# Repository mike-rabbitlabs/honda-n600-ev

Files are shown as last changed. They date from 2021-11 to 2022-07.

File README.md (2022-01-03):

# Honda N600 EV Conversion

All control systems and dash UI code.

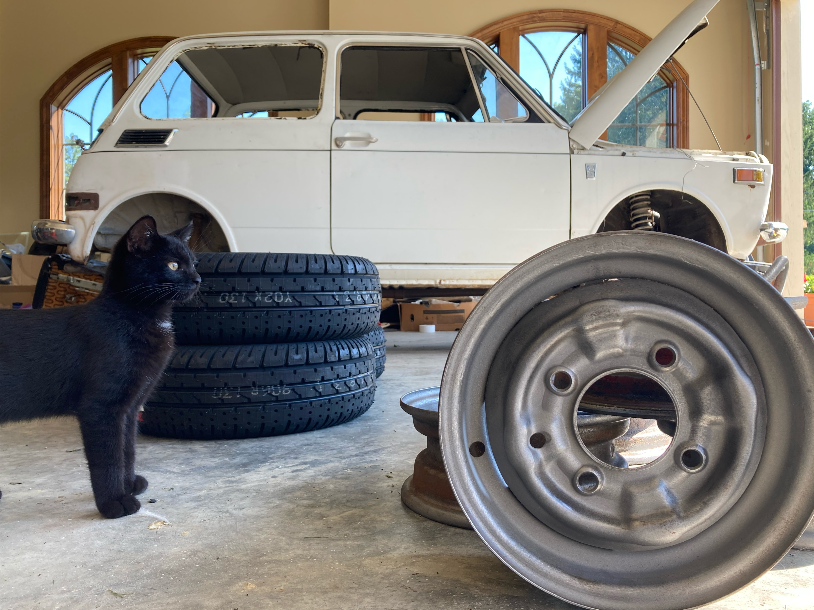
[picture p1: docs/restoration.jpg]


## Master Control Unit
Communicates (via CAN) to the BMS, controls fan, and coolant pumps, monitors temperature.

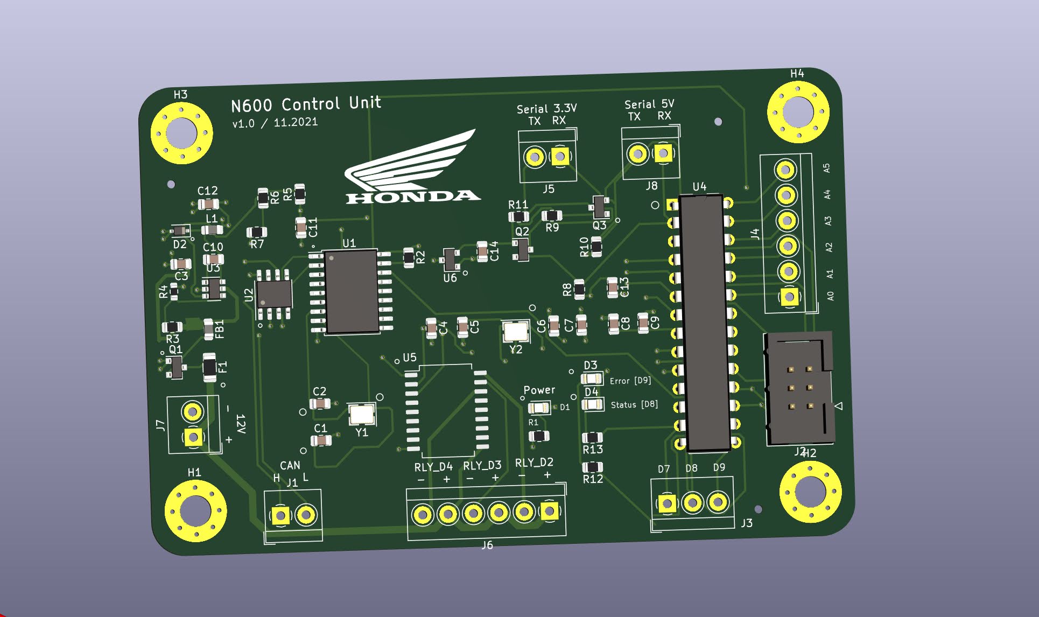
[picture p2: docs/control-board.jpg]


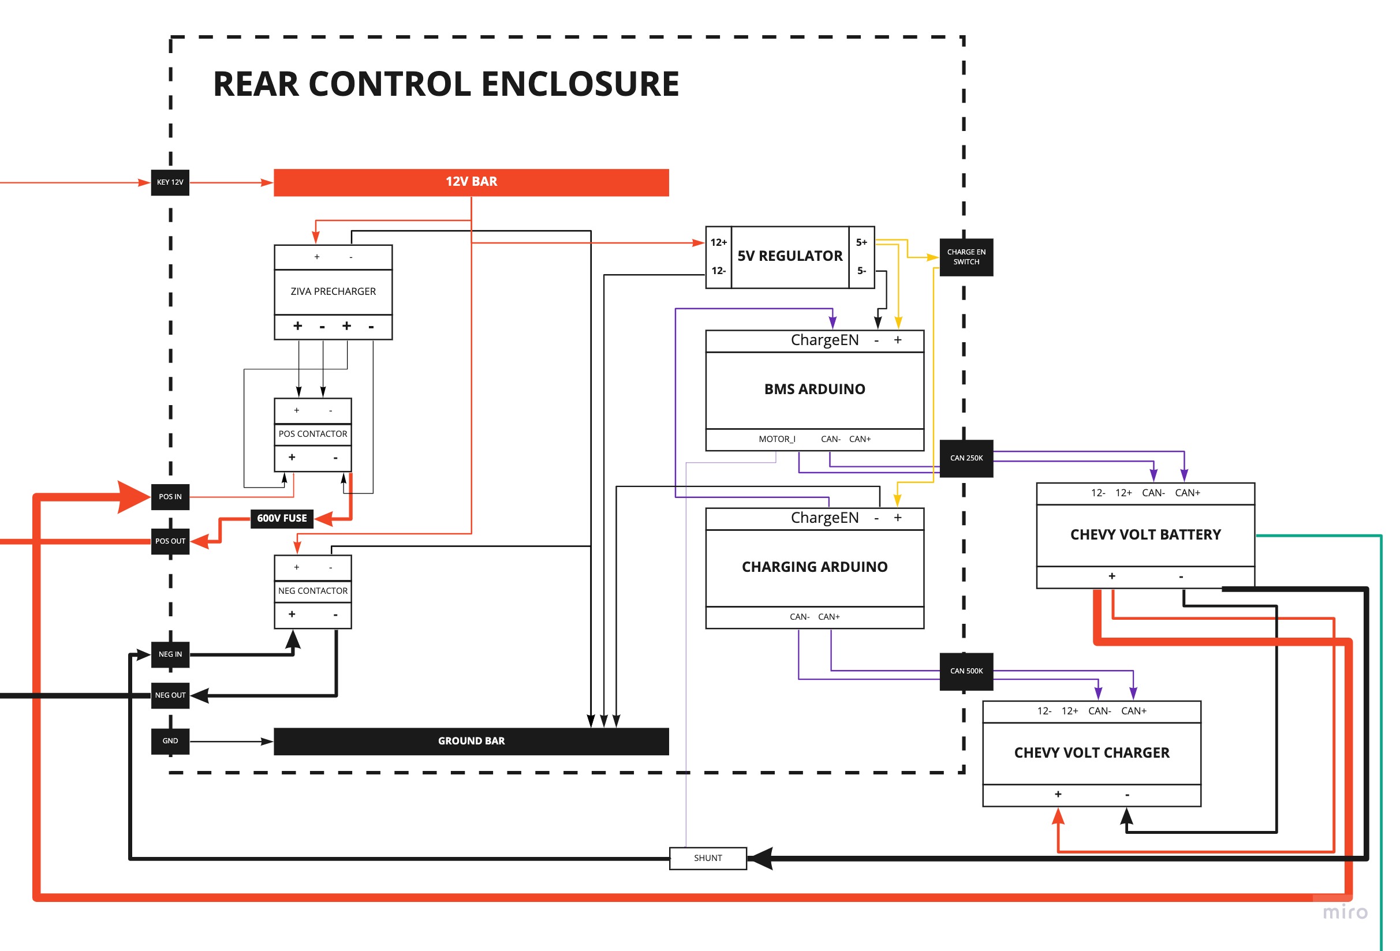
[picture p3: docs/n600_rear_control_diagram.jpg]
System Diagram


## Dash Screen UI

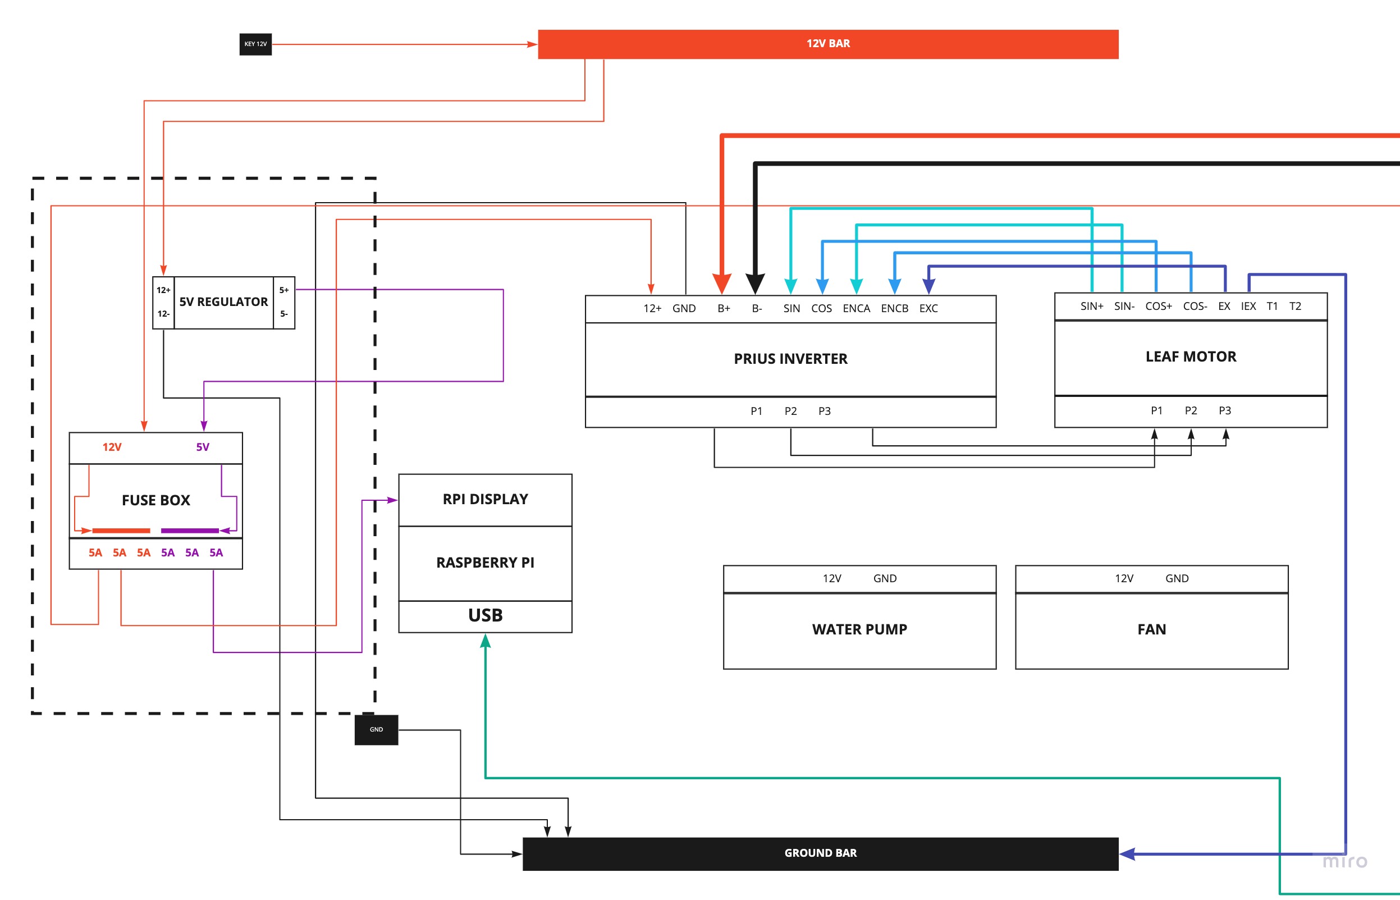
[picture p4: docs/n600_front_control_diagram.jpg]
System Diagram


### Requirements

* [Kikad](https://www.kicad.org/)
* [Node.js/NPM](https://nodejs.org/en/download/)

### Progress
* [Leaf EM61 Motor running with Prius Gen3 inverter](https://youtu.be/WkFnErgvj8M)
* [Raspberry Pi dash screen](https://youtu.be/67Cg47E4874)
* CAN communication with chevy volt bms
* CAN communication with chevy volt charger

### Dev Setup

* Within the dash-screen/server directory, Run: _npm install_ to download dependencies
* Within the dash-screen/ui directory, Run: _npm install_ to download dependencies
* Run: _npm start_ within the dash-screen/ui directory
* Run: _npm start_ within the dash-screen/server directory
* After the build process finishes, you should see a chrome popup to http://localhost:3001
* Frontend will auto reload on ui code changes

### Production Setup
* Build the app from within the dash-screen/server directory with: _npm run build_ (builds both the frontend and hosts from the compiled react app from the app server)
* The server should now host the react app at localhost:5000 (when running the server with _npm start_)
* Configure the docker-compose.yml file with your chose parameters, and run _docker-compose up_ to start the production server

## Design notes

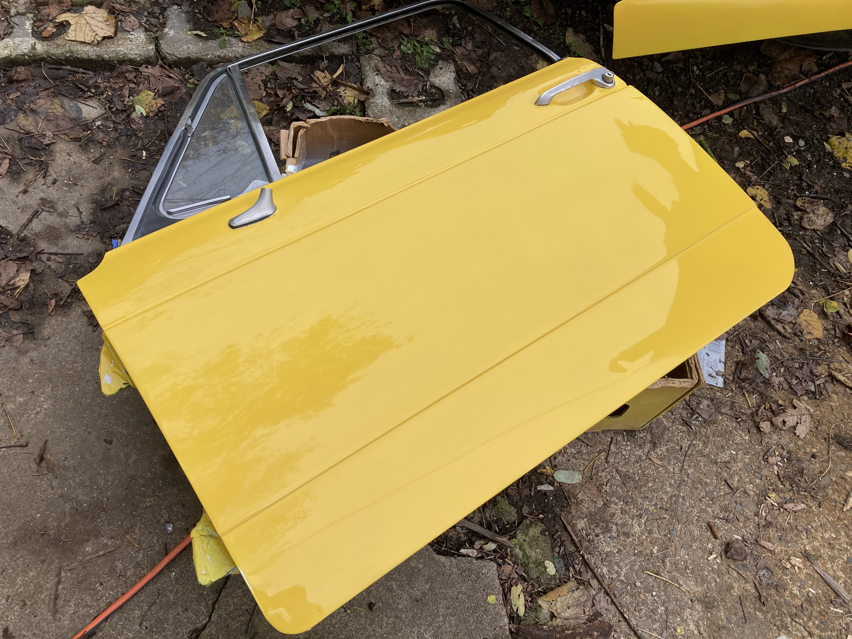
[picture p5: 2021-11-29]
docs/paint2.JPG

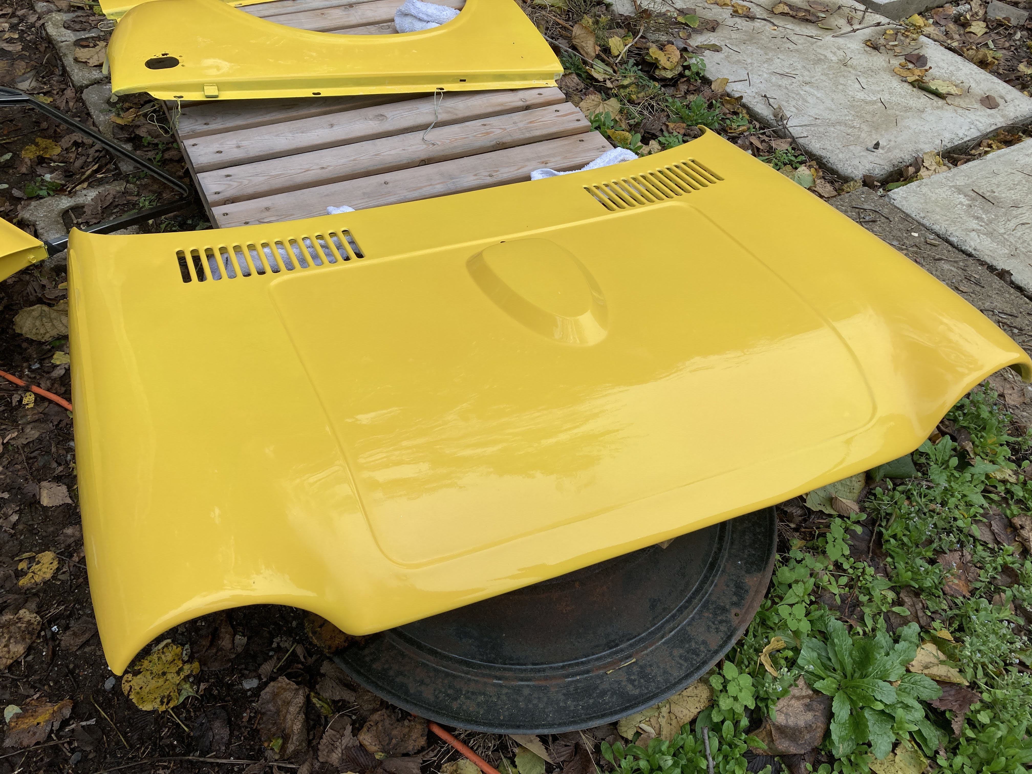
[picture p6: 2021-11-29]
docs/paint1.jpg

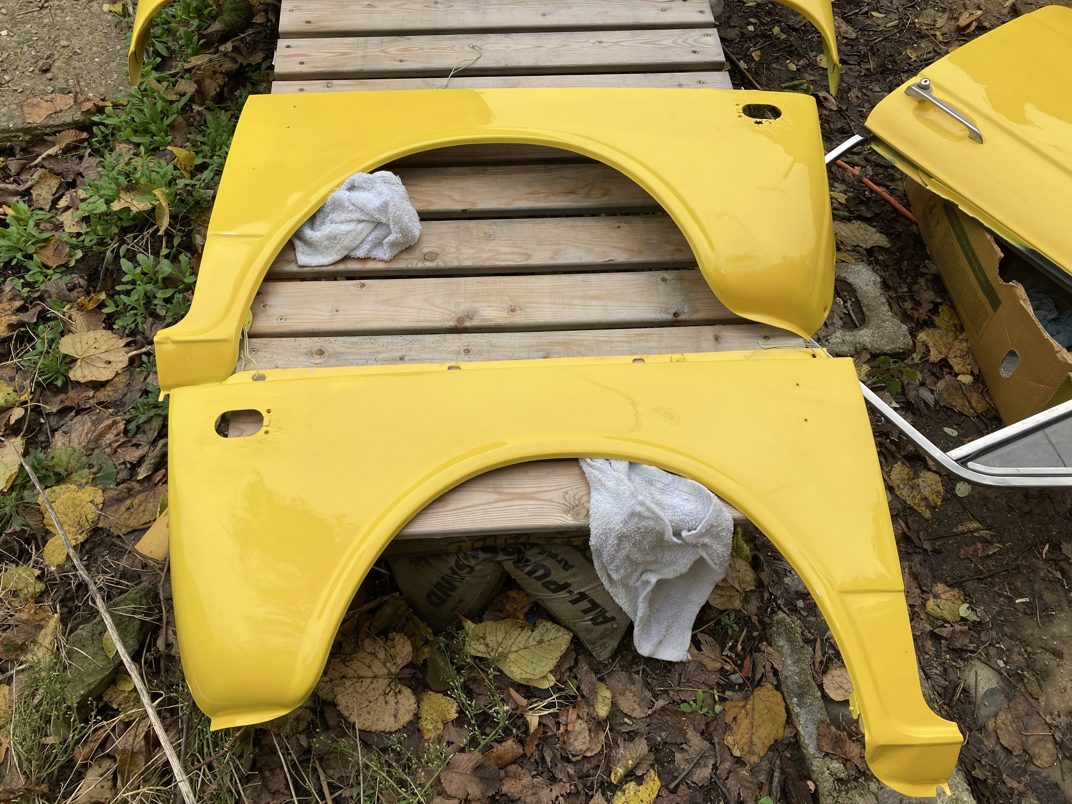
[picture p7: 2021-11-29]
docs/paint3.JPG

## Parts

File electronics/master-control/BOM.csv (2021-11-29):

Designator | Quantity | Comment | Footprint | Datasheet | JLCPCB Part #
C10 | 1 | 10nF | Capacitor_SMD:C_0805_2012Metric | ~ | C1710
C13 C14 | 2 | 1uF | Capacitor_SMD:C_0805_2012Metric | ~ | C28323
C3 C11 C12 | 3 | 10uF | Capacitor_SMD:C_0805_2012Metric | ~ | C15850
C1 C2 C4 C5 | 4 | 22pF | Capacitor_SMD:C_0805_2012Metric | ~ | C1804
C6 C7 C8 C9 | 4 | 100nF | Capacitor_SMD:C_0805_2012Metric | ~ | C49678
D1 D3 D4 | 3 | LED | LED_SMD:LED_0805_2012Metric | ~ | C84256
D2 | 1 | 1N5819 | Diode_SMD:D_SOD-323 | http://www.vishay.com/docs/88525/1n5817.pdf | C191023
F1 | 1 | 250mA | Fuse:Fuse_1206_3216Metric | ~ | C135334
FB1 | 1 | 600 @ 600Mhz | Inductor_SMD:L_0805_2012Metric | ~ | C1017
H1 H2 H3 H4 | 4 | MountingHole | MountingHole:MountingHole_4.3mm_M4_Pad_Via | ~
J1 J5 J7 J8 | 4 | Screw_Terminal_01x02 | TerminalBlock_4Ucon:TerminalBlock_4Ucon_1x02_P3.50mm_Horizontal | ~
J2 | 1 | AVR-ISP-6 | Connector_IDC:IDC-Header_2x03_P2.54mm_Vertical | ~
J3 | 1 | Screw_Terminal_01x03 | TerminalBlock_4Ucon:TerminalBlock_4Ucon_1x03_P3.50mm_Horizontal | ~
J4 J6 | 2 | Screw_Terminal_01x06 | TerminalBlock_4Ucon:TerminalBlock_4Ucon_1x06_P3.50mm_Horizontal | ~
L1 | 1 | 10u | Inductor_SMD:L_0805_2012Metric | ~ | C1046
Q1 | 1 | AO3401A | Package_TO_SOT_SMD:SOT-23 | http://www.aosmd.com/pdfs/datasheet/AO3401A.pdf | C15127
Q2 Q3 | 2 | 2N7002 | Package_TO_SOT_SMD:SOT-23 | https://www.onsemi.com/pub/Collateral/NDS7002A-D.PDF | C8545
R1 R12 R13 | 3 | 1.2K | Resistor_SMD:R_0805_2012Metric | ~ | C17379
R2 R8 R9 R10 R11 | 5 | 10K | Resistor_SMD:R_0805_2012Metric | ~ | C17414
R3 | 1 | 100K | Resistor_SMD:R_0603_1608Metric | ~ | C25803
R4 | 1 | 40K | Resistor_SMD:R_0603_1608Metric | ~ | C4197
R5 | 1 | 75K | Resistor_SMD:R_0805_2012Metric | ~ | C17819
R6 | 1 | 13K | Resistor_SMD:R_0805_2012Metric | ~ | C17455
R7 | 1 | 2.4K | Resistor_SMD:R_0805_2012Metric | ~ | C17526
U1 | 1 | MCP2515-xSO | Package_SO:SOIC-18W_7.5x11.6mm_P1.27mm | http://ww1.microchip.com/downloads/en/DeviceDoc/21801e.pdf
U2 | 1 | TJA1051T | Package_SO:SOIC-8_3.9x4.9mm_P1.27mm | http://www.nxp.com/documents/data_sheet/TJA1051.pdf | C6952
U3 | 1 | MP2359-DJ | Package_TO_SOT_SMD:SOT-23-6
U4 | 1 | ATmega328P-PU | Package_DIP:DIP-28_W7.62mm | http://ww1.microchip.com/downloads/en/DeviceDoc/ATmega328_P%20AVR%20MCU%20with%20picoPower%20Technology%20Data%20Sheet%2040001984A.pdf
U5 | 1 | ULN2803A | Package_SO:SOP-18_7x12.5mm_P1.27mm | http://www.ti.com/lit/ds/symlink/uln2803a.pdf | C845537
U6 | 1 | XC6206PxxxMR | Package_TO_SOT_SMD:SOT-23 | https://www.torexsemi.com/file/xc6206/XC6206.pdf | C5446
Y1 Y2 | 2 | 16Mhz | Crystal:Crystal_SMD_3225-4Pin_3.2x2.5mm | ~ | C13738

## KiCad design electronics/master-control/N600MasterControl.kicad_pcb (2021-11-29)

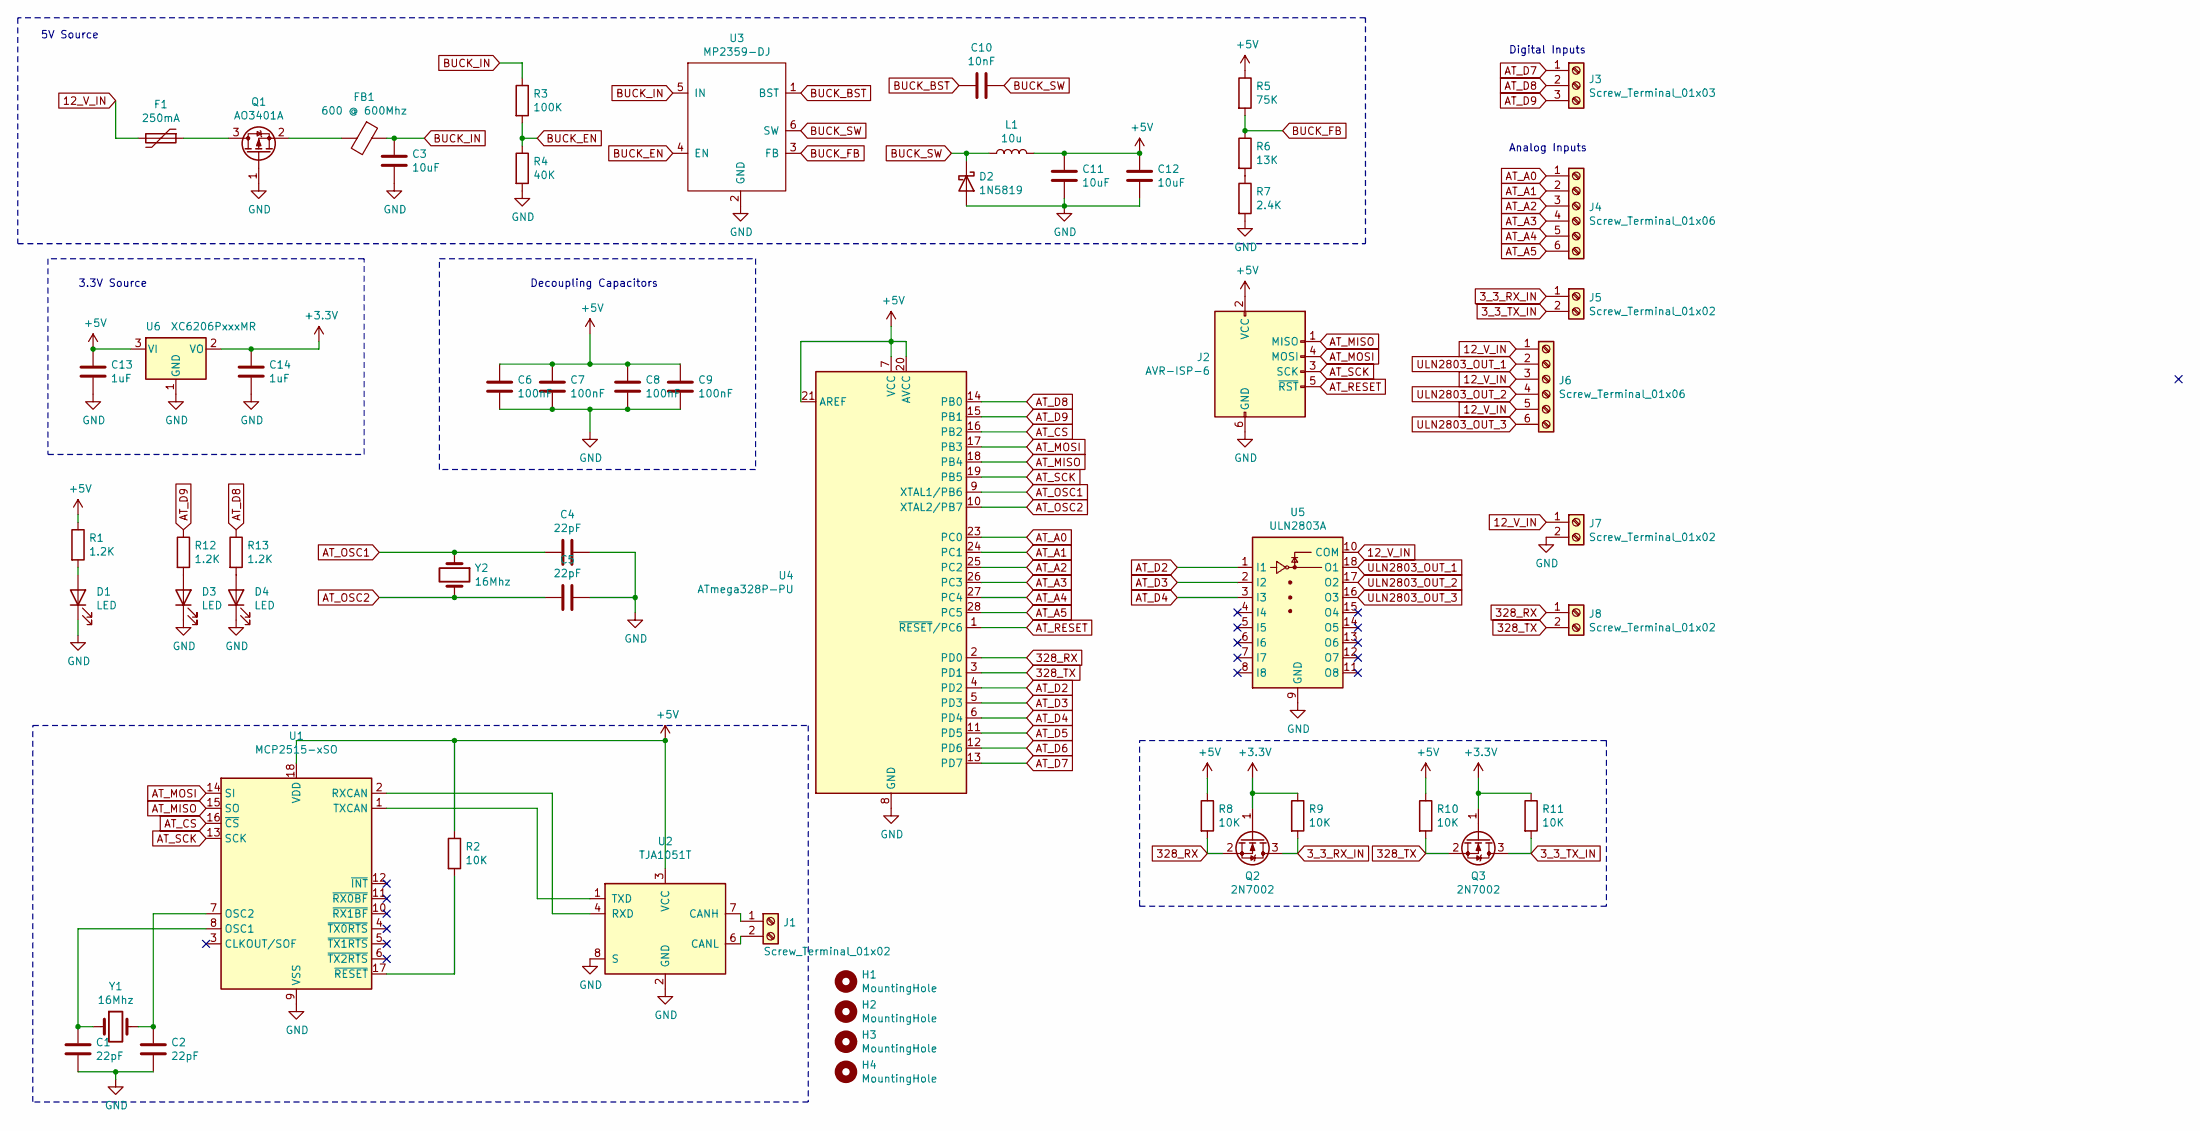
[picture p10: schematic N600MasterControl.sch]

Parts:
C1, C2, C4, C5: 22pF; C_0805_2012Metric; JLCPCB Part # C1804
C3, C11, C12: 10uF; C_0805_2012Metric; JLCPCB Part # C15850
C6, C7, C8, C9: 100nF; C_0805_2012Metric; JLCPCB Part # C49678
C10: 10nF; C_0805_2012Metric; JLCPCB Part # C1710
C13, C14: 1uF; C_0805_2012Metric; JLCPCB Part # C28323
D1: LED; LED_0805_2012Metric; JLCPCB Part # C84256
D2: 1N5819; D_SOD-323; JLCPCB Part # C191023
D3: LED; LED_0805_2012Metric; JLCPCB Part # C2297
D4: LED; LED_0805_2012Metric; JLCPCB Part # C2293
F1: 250mA; Fuse_1206_3216Metric; JLCPCB Part # C135334
FB1: 600 @ 600Mhz; L_0805_2012Metric; JLCPCB Part # C1017
H1, H2, H3, H4: MountingHole; MountingHole_4.3mm_M4_Pad_Via
J1, J5, J7, J8: Screw_Terminal_01x02; TerminalBlock_4Ucon_1x02_P3.50mm_Horizontal
J2: AVR-ISP-6; IDC-Header_2x03_P2.54mm_Vertical
J3: Screw_Terminal_01x03; TerminalBlock_4Ucon_1x03_P3.50mm_Horizontal
J4, J6: Screw_Terminal_01x06; TerminalBlock_4Ucon_1x06_P3.50mm_Horizontal
L1: 10u; L_0805_2012Metric; JLCPCB Part # C1046
Q1: AO3401A; SOT-23; JLCPCB Part # C15127
Q2, Q3: 2N7002; SOT-23; JLCPCB Part # C8545
R1, R12, R13: 1.2K; R_0805_2012Metric; JLCPCB Part # C17379
R2, R8, R9, R10, R11: 10K; R_0805_2012Metric; JLCPCB Part # C17414
R3: 100K; R_0603_1608Metric; JLCPCB Part # C25803
R4: 40K; R_0603_1608Metric; JLCPCB Part # C4197
R5: 75K; R_0805_2012Metric; JLCPCB Part # C17819
R6: 13K; R_0805_2012Metric; JLCPCB Part # C17455
R7: 2.4K; R_0805_2012Metric; JLCPCB Part # C17526
U1: MCP2515-xSO; SOIC-18W_7.5x11.6mm_P1.27mm
U2: TJA1051T; SOIC-8_3.9x4.9mm_P1.27mm; JLCPCB Part # C6952
U3: MP2359-DJ; SOT-23-6
U4: ATmega328P-PU; DIP-28_W7.62mm
U5: ULN2803A; SOP-18_7x12.5mm_P1.27mm; JLCPCB Part # C845537
U6: XC6206PxxxMR; SOT-23; JLCPCB Part # C5446
Y1, Y2: 16Mhz; Crystal_SMD_3225-4Pin_3.2x2.5mm; JLCPCB Part # C13738

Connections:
3_3_RX_IN: J5.1, Q2.3 (D), R9.2
3_3_TX_IN: J5.2, Q3.3 (D), R11.2
12_V_IN: F1.2, J6.1, J6.3, J6.5, J7.1, U5.10 (COM)
328_RX: J8.1, Q2.2 (S), R8.2, U4.2 (PD0)
328_TX: J8.2, Q3.2 (S), R10.2, U4.3 (PD1)
+3V3: C14.1, Q2.1 (G), Q3.1 (G), R9.1, R11.1, U6.2 (VO)
+5V: C6.1, C7.1, C8.1, C9.1, C11.1, C12.1, C13.1, J2.2 (VCC), L1.2, R1.1, R2.1, R5.1, R8.1, R10.1, U1.18 (VDD), U2.3 (VCC), U4.7 (VCC), U4.20 (AVCC), U4.21 (AREF), U6.3 (VI)
AT_A0: J4.1, U4.23 (PC0)
AT_A1: J4.2, U4.24 (PC1)
AT_A2: J4.3, U4.25 (PC2)
AT_A3: J4.4, U4.26 (PC3)
AT_A4: J4.5, U4.27 (PC4)
AT_A5: J4.6, U4.28 (PC5)
AT_CS: U1.16 (~CS), U4.16 (PB2)
AT_D2: U4.4 (PD2), U5.1 (I1)
AT_D3: U4.5 (PD3), U5.2 (I2)
AT_D4: U4.6 (PD4), U5.3 (I3)
AT_D5: U4.11 (PD5)
AT_D6: U4.12 (PD6)
AT_D7: J3.1, U4.13 (PD7)
AT_D8: J3.2, R13.1, U4.14 (PB0)
AT_D9: J3.3, R12.1, U4.15 (PB1)
AT_MISO: J2.1 (MISO), U1.15 (SO), U4.18 (PB4)
AT_MOSI: J2.4 (MOSI), U1.14 (SI), U4.17 (PB3)
AT_OSC1: C4.1, U4.9 (XTAL1/PB6), Y2.1
AT_OSC2: C5.1, U4.10 (XTAL2/PB7), Y2.2
AT_RESET: J2.5 (~RST), U4.1 (~RESET~/PC6)
AT_SCK: J2.3 (SCK), U1.13 (SCK), U4.19 (PB5)
BUCK_BST: C10.1, U3.1 (BST)
BUCK_EN: R3.2, R4.1, U3.4 (EN)
BUCK_FB: R5.2, R6.1, U3.3 (FB)
BUCK_IN: C3.1, FB1.1, R3.1, U3.5 (IN)
BUCK_SW: C10.2, D2.1 (K), L1.1, U3.6 (SW)
GND: C1.2, C2.2, C3.2, C4.2, C5.2, C6.2, C7.2, C8.2, C9.2, C11.2, C12.2, C13.2, C14.2, D1.1 (K), D2.2 (A), D3.1 (K), D4.1 (K), J2.6 (GND), J7.2, Q1.1 (G), R4.2, R7.2, U1.9 (VSS), U2.2 (GND), U2.8 (S), U3.2 (GND), U4.8 (GND), U4.22 (GND), U5.9 (GND), U6.1 (GND)
unnamed: C1.1, U1.8 (OSC1), Y1.1
unnamed: C2.1, U1.7 (OSC2), Y1.2
unnamed: D1.2 (A), R1.2
unnamed: D3.2 (A), R12.2
unnamed: D4.2 (A), R13.2
unnamed: F1.1, Q1.3 (D)
unnamed: FB1.2, Q1.2 (S)
unnamed: J1.1, U2.7 (CANH)
unnamed: J1.2, U2.6 (CANL)
unnamed: R2.2, U1.17 (~RESET)
unnamed: R6.2, R7.1
unnamed: U1.1 (TXCAN), U2.1 (TXD)
unnamed: U1.2 (RXCAN), U2.4 (RXD)
ULN2803_OUT_1: J6.2, U5.18 (O1)
ULN2803_OUT_2: J6.4, U5.17 (O2)
ULN2803_OUT_3: J6.6, U5.16 (O3)

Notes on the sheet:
Decoupling Capacitors
Analog Inputs
Digital Inputs
3.3V Source
5V Source

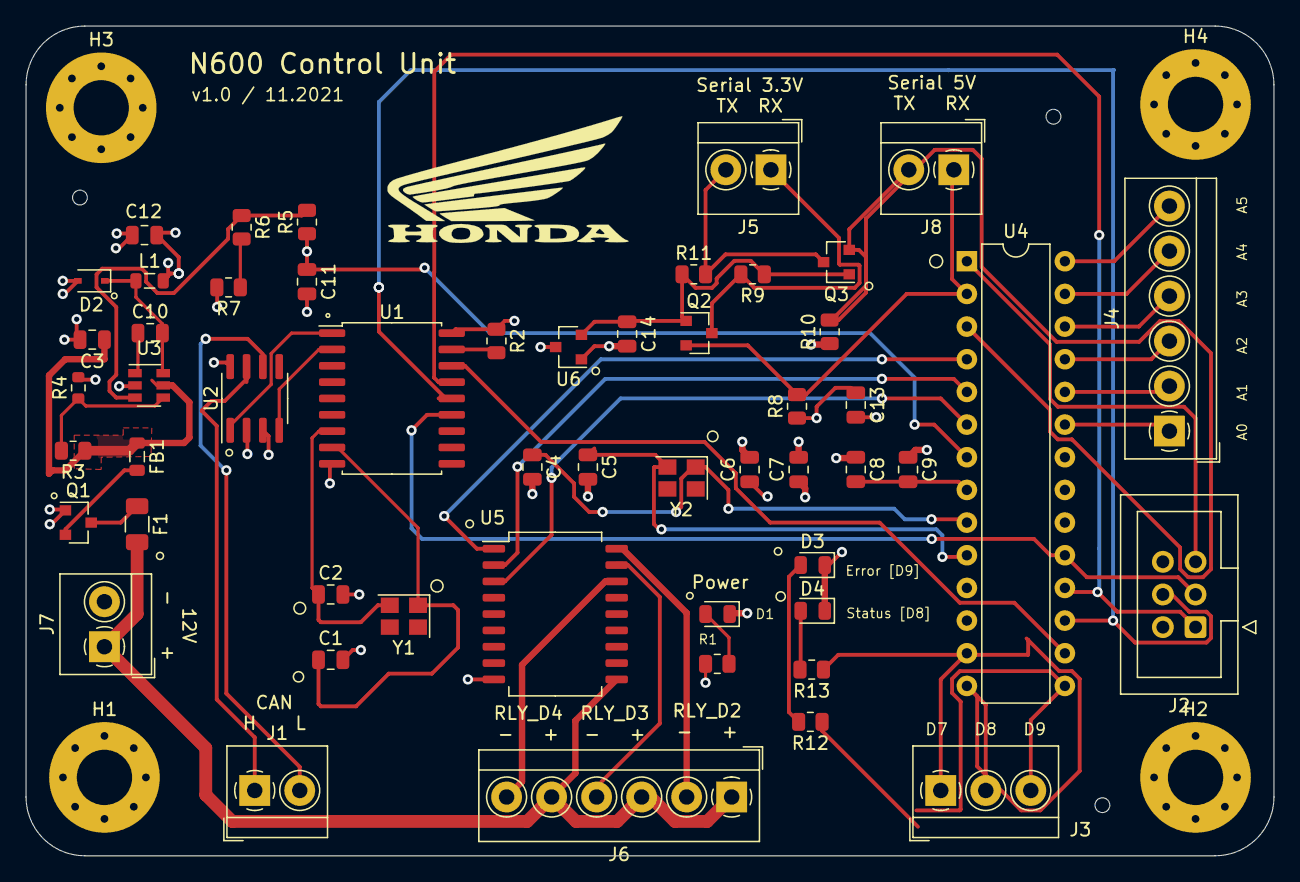
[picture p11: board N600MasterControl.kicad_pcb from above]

Board: 4 copper layers, 97.0 x 64.5 mm, 57 parts (0 on the bottom side), 48 nets.

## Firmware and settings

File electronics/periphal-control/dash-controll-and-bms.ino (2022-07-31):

#include <mcp_can.h>
#include <SPI.h>

#define SCREEN_ADDRESS 0x3C

#include <SPI.h>
#include <Wire.h>
#include <Adafruit_GFX.h>
#include <Adafruit_SSD1306.h>

#define SCREEN_WIDTH 128 // OLED display width, in pixels
#define SCREEN_HEIGHT 32 // OLED display height, in pixels

#define OLED_RESET     -1 // Reset pin # (or -1 if sharing Arduino reset pin)
#define SCREEN_ADDRESS 0x3C ///< See datasheet for Address; 0x3D for 128x64, 0x3C for 128x32
Adafruit_SSD1306 display(SCREEN_WIDTH, SCREEN_HEIGHT, &Wire, OLED_RESET);


uint16_t Cell[97]; //cells, raw 0.00125/V
uint16_t Temp[24]; // temperatures 0.0556/C and -27.778
uint16_t celllow, cellhigh, templow, temphigh;

long unsigned int rxId;
unsigned char len = 0;
unsigned char rxBuf[8];
uint8_t rxBufInt[8];
char msgString[128];                        // Array to store serial string

uint32_t tlast = 0;
int counter = 0;
float lastTotalVoltage = 1000;
float lastLowVoltage = 4000;
float celllowdisplay = 0;

#define CAN0_INT 2                              // Set INT to pin 2
MCP_CAN CAN0(10);                               // Set CS to pin 10

byte dataRequestBytes[8] = {0x02, 0x00, 0x00};


#define LOGO_HEIGHT   32
#define LOGO_WIDTH    128

static const unsigned char PROGMEM logo_bmp[] =
{ // 'honda-logo-62947-1944693', 128x32px
0x00, 0x00, 0x00, 0x00, 0x00, 0x00, 0x00, 0x00, 0x00, 0x00, 0x00, 0x00, 0x00, 0x00, 0x00, 0x00,
0x00, 0x00, 0x00, 0x00, 0x00, 0x00, 0x00, 0x00, 0x00, 0x00, 0x00, 0x00, 0x00, 0x00, 0x00, 0x00,
0x00, 0x00, 0x00, 0x08, 0x00, 0x00, 0x00, 0x00, 0x00, 0x00, 0x00, 0x00, 0x00, 0x00, 0x00, 0x00,
0x00, 0x00, 0x00, 0x38, 0x00, 0x00, 0x00, 0x00, 0x00, 0x00, 0x00, 0x00, 0x00, 0x00, 0x00, 0x00,
0x00, 0x00, 0x00, 0xf0, 0x00, 0x00, 0x00, 0x00, 0x00, 0x00, 0x00, 0x00, 0x00, 0x00, 0x00, 0x00,
0x00, 0x00, 0x07, 0xe0, 0x00, 0x00, 0x00, 0x00, 0x00, 0x00, 0x00, 0x00, 0x00, 0x00, 0x00, 0x00,
0x00, 0x00, 0x1f, 0x00, 0x00, 0x00, 0x00, 0x00, 0x00, 0x00, 0x00, 0x00, 0x00, 0x00, 0x00, 0x00,
0x00, 0x00, 0x78, 0x20, 0x00, 0x00, 0x00, 0x00, 0x00, 0x00, 0x00, 0x00, 0x00, 0x00, 0x00, 0x00,
0x00, 0x03, 0xc1, 0xc0, 0x00, 0x00, 0x00, 0x00, 0x00, 0x00, 0x00, 0x00, 0x00, 0x00, 0x00, 0x00,
0x00, 0x1e, 0x0f, 0x80, 0x00, 0x00, 0x00, 0x00, 0x00, 0x00, 0x00, 0x00, 0x00, 0x00, 0x00, 0x00,
0x00, 0x71, 0xf8, 0x01, 0xfe, 0x3f, 0xc3, 0xff, 0x87, 0xf8, 0x7e, 0xff, 0xfc, 0x07, 0xf8, 0x00,
0x03, 0xcf, 0xc3, 0x00, 0xf8, 0x1f, 0x0f, 0x87, 0xc3, 0xfc, 0x38, 0x3f, 0xff, 0x01, 0xfc, 0x00,
0x0e, 0x7c, 0x3f, 0x00, 0x78, 0x0e, 0x1f, 0x01, 0xe1, 0xfc, 0x18, 0x3c, 0x0f, 0x81, 0xfe, 0x00,
0x33, 0xe3, 0xfc, 0x00, 0x78, 0x0e, 0x1e, 0x01, 0xe1, 0xbe, 0x18, 0x3c, 0x07, 0x83, 0x9e, 0x00,
0x2f, 0x9f, 0x80, 0x00, 0x7f, 0xfe, 0x3e, 0x01, 0xf1, 0x9f, 0x18, 0x3c, 0x07, 0x83, 0x0f, 0x00,
0x31, 0xf0, 0x7c, 0x00, 0x7f, 0xfe, 0x3e, 0x01, 0xf1, 0x8f, 0x98, 0x3c, 0x07, 0x87, 0xff, 0x80,
0x1f, 0x9f, 0xf0, 0x00, 0x78, 0x0e, 0x1e, 0x01, 0xe1, 0x8f, 0x98, 0x3c, 0x07, 0x8f, 0xff, 0x80,
0x0d, 0xfe, 0x00, 0x00, 0x78, 0x0e, 0x1f, 0x01, 0xe1, 0x87, 0xf8, 0x3c, 0x07, 0x8c, 0x03, 0xc0,
0x07, 0xc3, 0x00, 0x00, 0xf8, 0x0f, 0x0f, 0x83, 0xc3, 0x83, 0xf8, 0x3e, 0x1f, 0x1c, 0x03, 0xe0,
0x03, 0x7f, 0xc0, 0x01, 0xfe, 0x3f, 0xc7, 0xff, 0x87, 0xe1, 0xf8, 0xff, 0xfe, 0x7f, 0x0f, 0xf8,
0x00, 0x00, 0x00, 0x00, 0x00, 0x00, 0x00, 0xfe, 0x00, 0x00, 0x00, 0x00, 0x00, 0x00, 0x00, 0x00,
0x00, 0x00, 0x00, 0x00, 0x00, 0x00, 0x00, 0x00, 0x00, 0x00, 0x00, 0x00, 0x00, 0x00, 0x00, 0x00,
0x00, 0x00, 0x00, 0x00, 0x00, 0x00, 0x00, 0x00, 0x00, 0x00, 0x00, 0x00, 0x00, 0x00, 0x00, 0x00,
0x00, 0x00, 0x00, 0x00, 0x00, 0x00, 0x00, 0x00, 0x00, 0x00, 0x00, 0x00, 0x00, 0x00, 0x00, 0x00,
0x00, 0x00, 0x00, 0x00, 0x00, 0x00, 0x00, 0x00, 0x00, 0x00, 0x00, 0x00, 0x00, 0x00, 0x00, 0x00,
0x00, 0x00, 0x00, 0x00, 0x00, 0x00, 0x00, 0x00, 0x00, 0x00, 0x00, 0x00, 0x00, 0x00, 0x00, 0x00,
0x00, 0x00, 0x00, 0x00, 0x00, 0x00, 0x00, 0x00, 0x00, 0x00, 0x00, 0x00, 0x00, 0x00, 0x00, 0x00,
0x00, 0x00, 0x00, 0x00, 0x00, 0x00, 0x00, 0x00, 0x00, 0x00, 0x00, 0x00, 0x00, 0x00, 0x00, 0x00,
0x00, 0x00, 0x00, 0x00, 0x00, 0x00, 0x00, 0x00, 0x00, 0x00, 0x00, 0x00, 0x00, 0x00, 0x00, 0x00,
0x00, 0x00, 0x00, 0x00, 0x00, 0x00, 0x00, 0x00, 0x00, 0x00, 0x00, 0x00, 0x00, 0x00, 0x00, 0x00,
0x00, 0x00, 0x00, 0x00, 0x00, 0x00, 0x00, 0x00, 0x00, 0x00, 0x00, 0x00, 0x00, 0x00, 0x00, 0x00,
0x00, 0x00, 0x00, 0x00, 0x00, 0x00, 0x00, 0x00, 0x00, 0x00, 0x00, 0x00, 0x00, 0x00, 0x00, 0x00 };


void setup()
{
  Serial.begin(115200);

  if(!display.begin(SSD1306_SWITCHCAPVCC, SCREEN_ADDRESS)) {
    Serial.println(F("SSD1306 allocation failed"));
    for(;;); // Don't proceed, loop forever
  }

  display.clearDisplay();
 
  // Initialize MCP2515 running at 16MHz with a baudrate of 500kb/s and the masks and filters disabled.
  if(CAN0.begin(MCP_ANY, CAN_125KBPS, MCP_8MHZ) == CAN_OK)
    Serial.println("MCP2515 Initialized Successfully!");
  else
    Serial.println("Error Initializing MCP2515...");
 
  CAN0.setMode(MCP_NORMAL);                     // Set operation mode to normal so the MCP2515 sends acks to received data.

  pinMode(CAN0_INT, INPUT);                            // Configuring pin for /INT input

  if(!display.begin(SSD1306_SWITCHCAPVCC, SCREEN_ADDRESS)) {
    Serial.println(F("SSD1306 allocation failed"));
    for(;;); // Don't proceed, loop forever
  }

  testdrawbitmap();

  delay(2000);
 
  display.clearDisplay();

  display.setTextSize(1);
  display.setTextColor(SSD1306_WHITE);
  display.setCursor(16,12);
  display.print(F("INITIALIZING."));
  display.display();
 
  delay(800);

  display.setCursor(16,12);
  display.print(F("INITIALIZING.."));
  display.display();

  delay(800);

  display.setCursor(16,12);
  display.print(F("INITIALIZING..."));
  display.display();

  sendDataRequest();
}

void loop()
{
  if(!digitalRead(CAN0_INT))                         // If CAN0_INT pin is low, read receive buffer
  {
    CAN0.readMsgBuf(&rxId, &len, rxBuf);      // Read data: len = data length, buf = data byte(s)
   
    if((rxId & 0x40000000) == 0x40000000){    // Determine if message is a remote request frame.
    } else {
      for(byte i = 0; i<len; i++){
          rxBufInt[i] = (unsigned int) (rxBuf[i]);
      }
      candecode(rxId, rxBufInt);
    }
  }


  if (tlast <  (millis() - 2000) && millis() > 2000) // 2hz loop
  {
    tlast = millis();
      printcells();
      updateScreen();
      if (counter % 5 == 0) {
       sendDataRequest();
      }
      counter += 1;
  }
}

void updateScreen() {

  if (celllowdisplay != 0) {
    float totalVoltage = 0.00;
    for (int y = 1; y < 97; y++)
    {
      totalVoltage += Cell[y] * 0.00125;
    }

    display.clearDisplay();

    display.setTextSize(1);             // Normal 1:1 pixel scale
    display.setTextColor(SSD1306_WHITE);        // Draw white text
    display.setCursor(95,0);
    display.println(F("RUN"));
    display.setCursor(95,12);
    if (celllowdisplay == 0) {
      display.println(F("---V"));
    } else {
      String lowestVoltageString = String(celllowdisplay, 2);
      display.println(lowestVoltageString + "V");
    }
    display.setCursor(95,24);
    display.println(F("89F"));
    display.display();
 
    display.setCursor(0,8);
    display.setTextSize(2);             // Draw 2X-scale text
    display.setTextColor(SSD1306_WHITE);

    if (totalVoltage < 200) {
      display.print("-----V");
    } else {
      String voltageString = String(totalVoltage, 1);
      display.print(voltageString + "V");
    }
 
    display.display();
  }
}

void sendDataRequest() {
  CAN0.sendMsgBuf(0x0200, 0, 3, dataRequestBytes);
}

void candecode(uint32_t canId, uint8_t* data)
{
  int t1 = (data[0] & 0x0F) << 8;
  int t1t = (data[0] & 0x03) << 8;
  int t2 = data[1];
  int t3 = (data[2] & 0x0F) << 8;
  int t3t = (data[2] & 0x03) << 8;
  int t4 = data[3];
  int t5 = (data[4] & 0x0F) << 8;
  int t6 = data[5];
  int t7 = (data[6] & 0x0F) << 8;
  int t8 = data[7];

  int x = 0;
  switch (canId)
  {
    case 0x460: //Module 1 cells 1-3
      Cell[1] = t1 + t2;
      Cell[2] = t3 + t4;
      Cell[3] = t5 + t6;
      break;
    case 0x470: //Module 1 cells 4-6
      Cell[4] = t1 + t2;
      Cell[5] = t3 + t4;
      Cell[6] = t5 + t6;
      break;
    case 0x461: //Module 1 cells 7-10
      Cell[7] = t1 + t2;
      Cell[8] = t3 + t4;
      Cell[9] = t5 + t6;
      Cell[10] = t7 + t8;
      break;
    case 0x471: //Module 1 cells 11-14
      Cell[11] = t1 + t2;
      Cell[12] = t3 + t4;
      Cell[13] = t5 + t6;
      Cell[14] = t7 + t8;
      break;
    case 0x462: //Module 1 cells 15-18
      Cell[15] = t1 + t2;
      Cell[16] = t3 + t4;
      Cell[17] = t5 + t6;
      Cell[18] = t7 + t8;
      break;
    case 0x472: //Module 1 cells 19-22
      Cell[19] = t1 + t2;
      Cell[20] = t3 + t4;
      Cell[21] = t5 + t6;
      Cell[22] = t7 + t8;
      break;
    case 0x463: //Module 1 cells 23-26
      Cell[23] = t1 + t2;
      Cell[24] = t3 + t4;
      Cell[25] = t5 + t6;
      Cell[26] = t7 + t8;
      break;
    case 0x473: //Module 1 cells 27-30
      Cell[27] = t1 + t2;
      Cell[28] = t3 + t4;
      Cell[29] = t5 + t6;
      Cell[30] = t7 + t8;
      break;
    case 0x464: //Module 2 cells 31-34
      Cell[31] = t1 + t2;
      Cell[32] = t3 + t4;
      Cell[33] = t5 + t6;
      Cell[34] = t7 + t8;
      break;
    case 0x474: //Module 2 cells 35-38
      Cell[35] = t1 + t2;
      Cell[36] = t3 + t4;
      Cell[37] = t5 + t6;
      Cell[38] = t7 + t8;
      break;
    case 0x465: //Module 2 cells 39-42
      Cell[39] = t1 + t2;
      Cell[40] = t3 + t4;
      Cell[41] = t5 + t6;
      Cell[42] = t7 + t8;
      break;
    case 0x475: //Module 2 cells 43-46
      Cell[43] = t1 + t2;
      Cell[44] = t3 + t4;
      Cell[45] = t5 + t6;
      Cell[46] = t7 + t8;
      break;
    case 0x466: //Module 2 cells 47-50
      Cell[47] = t1 + t2;
      Cell[48] = t3 + t4;
      Cell[49] = t5 + t6;
      Cell[50] = t7 + t8;
      break;
    case 0x476: //Module 2 cells 51-54
      Cell[51] = t1 + t2;
      Cell[52] = t3 + t4;
      Cell[53] = t5 + t6;
      Cell[54] = t7 + t8;
      break;
    case 0x468: //Module 3 cells 55-58
      Cell[55] = t1 + t2;
      Cell[56] = t3 + t4;
      Cell[57] = t5 + t6;
      Cell[58] = t7 + t8;
      break;
    case 0x478: //Module 3 cells 59-62
      Cell[59] = t1 + t2;
      Cell[60] = t3 + t4;
      Cell[61] = t5 + t6;
      Cell[62] = t7 + t8;
      break;
    case 0x469: //Module 3 cells 63-66
      Cell[63] = t1 + t2;
      Cell[64] = t3 + t4;
      Cell[65] = t5 + t6;
      Cell[66] = t7 + t8;
      break;
    case 0x479: //Module 3 cells 67-70
      Cell[67] = t1 + t2;
      Cell[68] = t3 + t4;
      Cell[69] = t5 + t6;
      Cell[70] = t7 + t8;
      break;
    case 0x46A: //Module 3 cells 71-74
      Cell[71] = t1 + t2;
      Cell[72] = t3 + t4;
      Cell[73] = t5 + t6;
      Cell[74] = t7 + t8;
      break;
    case 0x47A: //Module 3 cells 75-78
      Cell[75] = t1 + t2;
      Cell[76] = t3 + t4;
      Cell[77] = t5 + t6;
      Cell[78] = t7 + t8;
      break;

    case 0x46C: //Module 4 cells 79-81
      Cell[79] = t1 + t2;
      Cell[80] = t3 + t4;
      Cell[81] = t5 + t6;
      break;
    case 0x47C: //Module 4 cells 82-84
      Cell[82] = t1 + t2;
      Cell[83] = t3 + t4;
      Cell[84] = t5 + t6;
      break;
    case 0x46D: //Module 4 cells 85-87
      Cell[85] = t1 + t2;
      Cell[86] = t3 + t4;
      Cell[87] = t5 + t6;
      break;
    case 0x47D: //Module 4 cells 88-90
      Cell[88] = t1 + t2;
      Cell[89] = t3 + t4;
      Cell[90] = t5 + t6;
      break;
    case 0x46E: //Module 4 cells 91-93
      Cell[91] = t1 + t2;
      Cell[92] = t3 + t4;
      Cell[93] = t5 + t6;
      break;
    case 0x47E: //Module 4 cells 94-96
      Cell[94] = t1 + t2;
      Cell[95] = t3 + t4;
      Cell[96] = t5 + t6;
      break;

    case 0x7E0: //Module 1 Temp 1
      Temp[1] = t1t + t2;
      break;
    case 0x7E1: //Module 1 Temp 2
      Temp[2] = t1t + t2;
      break;
    case 0x7E2: //Module 1 Temp 3-4
      Temp[3] = t1t + t2;
      Temp[4] = t3t + t4;
      break;
    case 0x7E3: //Module 1 Temp 5
      Temp[5] = t1t + t2;
      break;

    case 0x7E4: //Module 2 Temp 6
      Temp[6] = t1t + t2;
      break;
    case 0x7E5: //Module 2 Temp 7-8
      Temp[7] = t1t + t2;
      Temp[8] = t3t + t4;
      break;
    case 0x7E6: //Module 2 Temp 9
      Temp[9] = t1t + t2;
      break;

    case 0x7E8: //Module 3 Temp 10
      Temp[10] = t1t + t2;
      break;
    case 0x7E9: //Module 3 Temp 11-12
      Temp[11] = t1t + t2;
      Temp[12] = t3t + t4;
      break;
    case 0x7EA: //Module 3 Temp 13
      Temp[13] = t1t + t2;
      break;

    case 0x7EC: //Module 4 Temp 14
      Temp[14] = t1t + t2;
      break;
    case 0x7ED: //Module 4 Temp 15
      Temp[15] = t1t + t2;
      break;
    case 0x7EE: //Module 4 Temp 16
      Temp[16] = t1t + t2;
      break;
  }
}

void printcells()
{
  int x = 0;
  cellhigh = 0;
  celllow = 4000; //5V / 0.00125
  Serial.println();
  Serial.println("Cell Voltages");
  for (int y = 1; y < 97; y++)
  {
    Serial.print(Cell[y] * 0.00125, 2);
    Serial.print(" | ");
    if (Cell[y] < celllow)
    {
      celllow = Cell[y];
    }
    if (Cell[y] > cellhigh)
    {
      cellhigh = Cell[y];
    }
    x++;
    if (x > 7)
    {
      x = 0;
      Serial.println();
    }
  }
  Serial.println();
  Serial.print("Lowest Cell: ");
  Serial.print(celllow * 0.00125, 2);
  Serial.print("  Highest Cell: ");
  Serial.print(cellhigh * 0.00125, 2);
  Serial.println();

  celllowdisplay = celllow * 0.00125;

  templow = 5000;
  temphigh = 0;
  x = 0;
  for (int y = 1; y < 17; y++)
  {
    Serial.print((Temp[y] * 0.0556) - 27.778, 2);
    Serial.print(" | ");
    if (Temp[y] < templow)
    {
      templow = Temp[y];
    }
    if (Temp[y] > temphigh)
    {
      temphigh = Temp[y];
    }
    x++;
    if (x > 7)
    {
      x = 0;
      Serial.println();
    }
  }
  Serial.println();
  Serial.print("Lowest Temp: ");
  Serial.print((templow * 0.0556) - 27.778, 2);
  Serial.print("  Highest Temp: ");
  Serial.print((temphigh * 0.0556) - 27.778, 2);
}

void testdrawbitmap(void) {
  display.clearDisplay();

  display.drawBitmap(
    (display.width()  - LOGO_WIDTH ) / 2,
    (display.height() - LOGO_HEIGHT) / 2,
    logo_bmp, LOGO_WIDTH, LOGO_HEIGHT, 1);
  display.display();
  delay(1000);
}

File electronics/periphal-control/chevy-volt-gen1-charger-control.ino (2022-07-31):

#include <mcp_can.h>
#include <SPI.h>
#define CAN0_INT 2

MCP_CAN CAN0(10);


int canInitialized  = -1;

const int CHARGER_HEARTBEAT_INTERVAL_MS = 30;
const int CHARGER_CONFIG_INTERVAL_MS = 500;

const int CHARGE_CURRENT_A_HEX = 0x10; // 0x8 is 0.4A, 0x10 is 0.8A. Multiply amps by 20 and convert to hex
const int CHARGE_TARGET_VOLTAGE = 382; // Multiply amps by 20 and convert to hex
const int CHARGE_END_CURRENT = 0.4; // Stop charging when it's at 0.4 amp

uint16_t Vol_temp=0;

unsigned long lastSwitchTime;
unsigned long lastHeartbeatTime;
unsigned long lastChargeConfigCommandTime;

byte heartbeatBytes[1] = { 0x03 }; // 0x01 only 12V charging, 0x02 only HV, 0x03 HV and 12V
byte chargeCommandBytes[4] = { 0x00, 0x00, 0x00, 0x00 };

long unsigned int rxId;
unsigned char len = 0;

uint8_t rxBufInt[8];
uint8_t rxBuf[8];

boolean indicatorLEDOn;
boolean isCharging = false;
boolean hasInitializedCharging = false;

int currentCommand = -1;

float HVcur=0;
float HVvol=0;
float ACcur=0;
float ACvol=0;
float LVcur=0;
float LVvol=0;

void setup() {
  Serial.begin(115200);
  while (!Serial) {
    ; // wait for serial port to connect. Needed for Native USB only
  }

  pinMode(CAN0_INT, INPUT);

  if(CAN0.begin(MCP_ANY, CAN_500KBPS, MCP_8MHZ) == CAN_OK){
    Serial.println("MCP2515 Initialized Successfully!");
    canInitialized = 1;
  } else {
    Serial.println("Error Initializing MCP2515...");
    canInitialized = 0;
  }

  CAN0.setMode(MCP_NORMAL);
}

void loop() {

  if (!digitalRead(CAN0_INT)) {
   CAN0.readMsgBuf(&rxId, &len, rxBuf);

   if ((rxId & 0x40000000) == 0x40000000) {
   
   } else {
    for (byte i = 0; i < len; i++) {
      rxBufInt[i] = (unsigned int) (rxBuf[i]);
    }

    if (rxId == 0x212) {
          uint16_t HVcur_temp = (uint16_t)(rxBuf[0]<<8 | rxBuf[1]);
          HVcur = (float)(HVcur_temp>>3)*0.05;
         
         uint16_t HVvol_temp = (uint16_t)((((rxBuf[1]<<8 | rxBuf[2]))>>1)&0x3ff);
           HVvol = (float)(HVvol_temp)*.5;
           
         uint16_t LVcur_temp = (uint16_t)(((rxBuf[2]<<8 | rxBuf[3])>>1)&0x00ff);
          LVcur = (float)(LVcur_temp)*.2;

         
          uint16_t LVvol_temp = (uint16_t)(((rxBuf[3]<<8 | rxBuf[4])>>1)&0x00ff);
          LVvol = (float)(LVvol_temp)*.1;

          if (HVcur < CHARGE_END_CURRENT) {
            isCharging = false;
          }
    }

    if (rxId == 0x30A) {
         uint16_t ACcur_temp = (uint16_t)((rxBuf[0]<<8 | rxBuf[1])>>4);
         ACcur = (float)(ACcur_temp)*0.2;
         
         uint16_t ACvol_temp = (uint16_t)(((rxBuf[1]<<8 | rxBuf[2])>>4)&0x00ff);
         ACvol = (float)(ACvol_temp)*2;
    }
   }
  }


  if (millis() - lastSwitchTime > 1000) {
    lastSwitchTime = millis();
    Serial.print("HV-V=");
    Serial.print(HVvol);
    Serial.print(", HV-A=");
    Serial.print(HVcur);
    Serial.print(", AC-V=");
    Serial.print(ACvol);
    Serial.print(", AC-A=");
    Serial.print(ACcur);
    Serial.print(", LV-V=");
    Serial.print(LVvol);
    Serial.print(", LV-A=");
    Serial.print(LVcur);
    Serial.print(", CANINIT=");
    Serial.println(canInitialized);
    if (ACvol >= 1 && !isCharging && !hasInitializedCharging) {
        // AC CONNECTED FOR THE FIRST TIME
        isCharging = true;
        hasInitializedCharging = true;
    }
  }


  if (millis() - lastHeartbeatTime > CHARGER_HEARTBEAT_INTERVAL_MS) {
    if (isCharging) {
      lastHeartbeatTime = millis();

      CAN0.sendMsgBuf(0x30E, 0, 1, heartbeatBytes);
    }
  }

  if (millis() - lastChargeConfigCommandTime > CHARGER_CONFIG_INTERVAL_MS) {
    if (isCharging) {
      lastChargeConfigCommandTime = millis();

      int Vol_temp=CHARGE_TARGET_VOLTAGE*2;
      chargeCommandBytes[0] = 0x40;
      chargeCommandBytes[1] = CHARGE_CURRENT_A_HEX;
      chargeCommandBytes[2] = highByte(Vol_temp);
      chargeCommandBytes[3] = lowByte(Vol_temp);
      CAN0.sendMsgBuf(0x304, 0, 4, chargeCommandBytes);
    }
  }
}

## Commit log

2022-01-03 Adding CAN control scripts for chevy volt charger and bms
    Work left:
    • Integrate bms and charging code
    • Ensure we don't charge if we're running
    • Add BMS balancing commands to volt code
2022-07-31 Adding newest arduino control software
